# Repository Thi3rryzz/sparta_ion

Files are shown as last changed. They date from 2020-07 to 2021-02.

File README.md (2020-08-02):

Open Source Sparta ION
=============
There's a bunch of (Dutch) blog posts that go with this: (http://infant.tweakblogs.net/blog/cat/2875) (Awesome work InfantEudora)
Also check out the Discord: (https://discord.gg/anZees2)

This repository contains the following:

 folder       |  descr
--------------|-------------------------------------------------------------
 eagle        | All relevant eagle files, BOM lists.
 ion_firmware | AVR Studio projects for the different kinds of firmware.
 ion_software | Software for testing, or uploading hex files.
 lib          | Files used in either firmware or software.
 lib_ion      | Files used for Sparta ION specific code.

All files in this repository are released under GNU GPLv3 (https://www.gnu.org/copyleft/gpl.html)

Software used:
----------------
 - Atmel Studio 7.0.2397 (https://www.microchip.com/mplab/avr-support/atmel-studio-7)
 - GCC 9.3.0
 - Windows: Cygwin(https://cygwin.com/install.html)
 - Eagle 8.6.3 (http://www.cadsoftusa.com/)

Firmware:
----------------

The firmware running your bike's motor, consists of three parts:
 - A bootloader, started on powerup.
 - The actual firmware, called application executed by the bootloader.
 - Configuration memory, stored in ROM.

The bootloader uses two blocks to identify the harware it's running on, and what firmware should be loaded.
The firware uses one block to read/write settings, which are currently the strain gauge calibration.

If you wan't to build a control PCB, use the latest revision of 3phasecntrl.

New Hardare Revision Wishlist:
Motor Driver:
 - Modify 3phasecntrl for XHP motors.
BMS:
 - Modifiy BMS for Li-Ion/Li-Po support.

New Software Revision Wishlist:
 - Enhance CU3 Display support
 - Write BMS code
 - Modify Bootloader for BMS

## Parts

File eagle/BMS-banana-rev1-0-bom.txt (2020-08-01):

Part          Value                            Device                           Package              Description                             FARNELL LCSC    LSCS   MPN        OC_FARNELL OC_NEWARK PACKAGE               POPULARITY SPICEPREFIX SUPPLIER              
C1            4u7                              C-EUC0805                        C0805                CAPACITOR, European symbol                                                                                           88         C                                 
C2            100n                             C-EUC0805                        C0805                CAPACITOR, European symbol                                                                                           88         C                                 
C3            100n                             C-EUC0805                        C0805                CAPACITOR, European symbol                                                                                           88         C                                 
C4            22p                              C-EUC0805                        C0805                CAPACITOR, European symbol                                                                                           88         C                                 
C5            22p                              C-EUC0805                        C0805                CAPACITOR, European symbol                                                                                           88         C                                 
C6            10u/50V                          CPOL-EU153CLV-0605               153CLV-0605          POLARIZED CAPACITOR, European symbol                                                                                                                              
C7            33u/25V                          CPOL-EU153CLV-0605               153CLV-0605          POLARIZED CAPACITOR, European symbol                                                                                                                              
C8            10u/16V                          CPOL-EU153CLV-0405               153CLV-0405          POLARIZED CAPACITOR, European symbol                                                                                                                              
C9            1u                               C-EUC0805                        C0805                CAPACITOR, European symbol                                                                                           88         C                                 
C10           100n                             C-EUC0805                        C0805                CAPACITOR, European symbol                                                                                           88         C                                 
C11           10u/16V                          CPOL-EU153CLV-0405               153CLV-0405          POLARIZED CAPACITOR, European symbol                                                                                                                              
C12           100n                             C-EUC0805                        C0805                CAPACITOR, European symbol                                                                                           88         C                                 
C13           100n                             C-EUC0805                        C0805                CAPACITOR, European symbol                                                                                           88         C                                 
C14           100n                             C-EUC0805                        C0805                CAPACITOR, European symbol                                                                                           88         C                                 
C15           22u/16V                          C-EUC0805                        C0805                CAPACITOR, European symbol                                                                                           88         C                                 
C16           22u/16V                          C-EUC0805                        C0805                CAPACITOR, European symbol                                                                                           88         C                                 
C17           100n                             C-EUC0805                        C0805                CAPACITOR, European symbol                                                                                           88         C                                 
C18           22u/16V                          C-EUC0805                        C0805                CAPACITOR, European symbol                                                                                           88         C                                 
C19           100n                             C-EUC0805                        C0805                CAPACITOR, European symbol                                                                                           88         C                                 
C20           100n                             C-EUC0805                        C0805                CAPACITOR, European symbol                                                                                           88         C                                 
C21           100n                             C-EUC0805                        C0805                CAPACITOR, European symbol                                                                                           88         C                                 
C22           22p                              C-EUC0805                        C0805                CAPACITOR, European symbol                                                                                           88         C                                 
C23           DNP                              C-EUC0805                        C0805                CAPACITOR, European symbol                                                                                           88         C                                 
D1            BAT46WH                          DIODE-SMB                        SMB                  DIODE                                   2069340                                                                                                                   
D2            BAT46WH                          DIODE-SMB                        SMB                  DIODE                                   2069340                                                                                                                   
D3            BAT46WH                          DIODE-SMB                        SMB                  DIODE                                   2069340                                                                                                                   
D4            SM6T39A                          DIODE-SMB                        SMB                  DIODE                                   9802703                                                                                                                   
D5            BAT46WH                          DIODE-SOD323-W                   SOD323-W             DIODE                                                                                                                                                             
F1            1A                               PTCFUSE-1812                     1812                 PTC fuses, resettable thermistors                                                                                                                                 
F2            300mA                            PTCFUSE-1812                     1812                 PTC fuses, resettable thermistors                                                                                                                                 
F3            300mA                            PTCFUSE-1812                     1812                 PTC fuses, resettable thermistors                                                                                                                                 
IC4           LD1117S50                        LM340ST-ST                       SOT223               Positive VOLTAGE REGULATOR              1467780                                                                                                                   
IC6           LD1117S33                        LM340ST-ST                       SOT223               Positive VOLTAGE REGULATOR                                                                                                                                        
K1            SLA-12VDC-SL-A                   SLA-12VDC-SL-A                   SLA-12VDC-SL-A                                                               C55194                                                                                                    
K2            SLA-12VDC-SL-A                   SLA-12VDC-SL-A                   SLA-12VDC-SL-A                                                               C55194                                                                                                    
L1            150u/250mA                       L-USWE-TPC                       POWER-CHOKE_WE-TPC   INDUCTOR, American symbol                                                                                                                                         
L2            4.7uH/700mA                      L_0805                           L0805                                                                                                                                                                                  
LED1          Red                              LEDCHIPLED_0805                  CHIPLED_0805         LED                                                                                                                  52                                           
LED2          Green                            LEDCHIPLED_0805                  CHIPLED_0805         LED                                                                                                                  52                                           
Q1            2N7002                           2N7002                           SOT-23                                                                                                                                                                                 
Q2            2N7002                           2N7002                           SOT-23                                                                                                                                                                                 
Q3            Q13FC1350000400                  Q13FC1350000400                  CRYSTAL_3215                                                         C32346                                                                                                            
R1            1k                               R-EU_R0805                       R0805                RESISTOR, European symbol                                                                                            86         R                                 
R2            2R2                              R-EU_R0805                       R0805                RESISTOR, European symbol                                                                                            86         R                                 
R3            10r                              R-EU_R0805                       R0805                RESISTOR, European symbol                                                                                            86         R                                 
R4            390k                             R-EU_R0805                       R0805                RESISTOR, European symbol                                                                                            86         R                                 
R5            100k                             R-EU_R0805                       R0805                RESISTOR, European symbol                                                                                            86         R                                 
R6            1k                               R-EU_R0805                       R0805                RESISTOR, European symbol                                                                                            86         R                                 
R7            1k                               R-EU_R0805                       R0805                RESISTOR, European symbol                                                                                            86         R                                 
R8            4k7                              R-EU_R0805                       R0805                RESISTOR, European symbol                                                                                            86         R                                 
R9            100k                             R-EU_R0805                       R0805                RESISTOR, European symbol                                                                                            86         R                                 
R10           4k7                              R-EU_R0805                       R0805                RESISTOR, European symbol                                                                                            86         R                                 
R11           10k                              R-EU_R0805                       R0805                RESISTOR, European symbol                                                                                            86         R                                 
R12           10k                              R-EU_R0805                       R0805                RESISTOR, European symbol                                                                                            86         R                                 
R13           16k2                             R-EU_R0805                       R0805                RESISTOR, European symbol                                                                                            86         R                                 
R14           604k                             R-EU_R0805                       R0805                RESISTOR, European symbol                                                                                            86         R                                 
R15           5m 4W                            SHUNT_2728                       R2728                                                                                                                                                                                  
R16           10k                              R-EU_R0805                       R0805                RESISTOR, European symbol                                                                                            86         R                                 
R17           100r                             R-EU_R0805                       R0805                RESISTOR, European symbol                                                                                            86         R                                 
R18           100r                             R-EU_R0805                       R0805                RESISTOR, European symbol                                                                                            86         R                                 
R19           10k                              R-EU_R0805                       R0805                RESISTOR, European symbol                                                                                            86         R                                 
R20           1k                               R-EU_R0805                       R0805                RESISTOR, European symbol                                                                                            86         R                                 
R22           20k                              R-EU_R0805                       R0805                RESISTOR, European symbol                                                                                            86         R                                 
R23           130k                             R-EU_R0805                       R0805                RESISTOR, European symbol                                                                                            86         R                                 
R24           10k                              R-EU_R0805                       R0805                RESISTOR, European symbol                                                                                            86         R                                 
R25           10k                              R-EU_R0805                       R0805                RESISTOR, European symbol                                                                                            86         R                                 
R26           390k                             R-EU_R0805                       R0805                RESISTOR, European symbol                                                                                            86         R                                 
R27           100k                             R-EU_R0805                       R0805                RESISTOR, European symbol                                                                                            86         R                                 
R28           390k                             R-EU_R0805                       R0805                RESISTOR, European symbol                                                                                            86         R                                 
R29           220k                             R-EU_R0805                       R0805                RESISTOR, European symbol                                                                                            86         R                                 
R30           100r                             R-EU_R0805                       R0805                RESISTOR, European symbol                                                                                            86         R                                 
R31           100r                             R-EU_R0805                       R0805                RESISTOR, European symbol                                                                                            86         R                                 
R32           100k                             R-EU_R0805                       R0805                RESISTOR, European symbol                                                                                            86         R                                 
R33           100k                             R-EU_R0805                       R0805                RESISTOR, European symbol                                                                                            86         R                                 
R34           1k                               R-EU_R0805                       R0805                RESISTOR, European symbol                                                                                            86         R                                 
R35           1k                               R-EU_R0805                       R0805                RESISTOR, European symbol                                                                                            86         R                                 
R36           10k                              R-EU_R0805                       R0805                RESISTOR, European symbol                                                                                            86         R                                 
R37           10k                              R-EU_R0805                       R0805                RESISTOR, European symbol                                                                                            86         R                                 
R38           10k                              R-EU_R0805                       R0805                RESISTOR, European symbol                                                                                            86         R                                 
R40           3k9                              R-EU_R0805                       R0805                RESISTOR, European symbol                                                                                            86         R                                 
R41           10k                              R-EU_R0805                       R0805                RESISTOR, European symbol                                                                                            86         R                                 
R43           1k                               R-EU_R0805                       R0805                RESISTOR, European symbol                                                                                            86         R                                 
RT1           NTC_0805                         NTC_0805                         R0805                                                                                                                                                                                  
T1            BC847                            BC847                            SOT23                NPN TRANSISTOR                                                                                                                                                    
T2            BC847                            BC847                            SOT23                NPN TRANSISTOR                                                                                                                                                    
U$1           AVR-PDIVERT                      AVR-PDIVERT                      AVR-ISP-6            AVR PDI programming interface connector                                                                                                                           
U$2           TSX-3225                         TSX-3225                         TSX-3225                                                                                                                                                                               
U1            ATXMEGA32A4U-AU                  ATXMEGA32A4U-AU                  TQFP-44A-44          8/16-bit XMEGA A4U Microcontroller                                                                                                                                
U2            LM5008MM                         LM5008MM                         SOP65P490X109-8N     Step-Down Switching Regulator                                  LM5008MM   8181721    38K3760   SOP-8                                        National Semiconductor
U3            BQ34Z100                         BQ34Z100                         PW_R-PDSO-G14                                                                                                                                                                          
U4            JW5033S                          JW5033S                          SOT23-6                                                              C324577                                                                                                           
U5            PCF8563                          PCF8563                          SO08                                                                 C7440                                                                                                             
U6            90325-0008                       90325-0008                       MOLEX_90325-0008     HEADER                                                         90325-0008 673237     46WX960   HEADER, 1.27MM, 8 WAY                        Molex

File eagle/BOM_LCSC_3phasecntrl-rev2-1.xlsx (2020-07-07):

LCSC Part Number | Manufacture Part Number | Manufacturer | Customer NO. | Package | Description | RoHS | Order Qty. | Min\Mult Order Qty. | Unit Price | Order Price
C1779 | CL21A475KAQNNNE | Samsung Electro-Mechanics |  | 0805 | Multilayer Ceramic Capacitors MLCC - SMD/SMT 4.7uF 25V 0805 RoHS | Yes | 20 | 20\20 | $0.016685 | $0.33
C2316 | XH-3A | BOOMELE(Boom Precision Elec) |  | Through Hole | Wire To Board / Wire To Wire Connector Through Hole RoHS | Yes | 50 | 50\50 | $0.00584 | $0.29
C2318 | XH-5A | BOOMELE(Boom Precision Elec) |  | Through Hole | Wire To Board / Wire To Wire Connector Through Hole RoHS | Yes | 50 | 50\50 | $0.009577 | $0.48
C5670 | XH-T | BOOMELE(Boom Precision Elec) |  | - | Terminals RoHS | Yes | 200 | 100\100 | $0.003339 | $0.67
C10384 | XH-7A | BOOMELE(Boom Precision Elec) |  | Through Hole | Wire To Board / Wire To Wire Connector Through Hole RoHS | Yes | 50 | 50\50 | $0.01369 | $0.68
C10387 | XH-3Y | BOOMELE(Boom Precision Elec) |  | Housing | Rectangular Connectors Housings Housing RoHS | Yes | 100 | 100\100 | $0.002335 | $0.23
C10388 | XH-5Y | BOOMELE(Boom Precision Elec) |  | Housing | Rectangular Connectors Housings Housing RoHS | Yes | 50 | 50\50 | $0.004063 | $0.2
C16906 | XH-7Y | BOOMELE(Boom Precision Elec) |  | Housing | Rectangular Connectors Housings Housing RoHS | Yes | 50 | 50\50 | $0.005804 | $0.29
C17656 | 0805W8F3903T5E | UNI-ROYAL(Uniroyal Elec) |  | 0805 | Chip Resistor - Surface Mount 390KOhms ±1% 1/8W 0805 RoHS | Yes | 100 | 100\100 | $0.002323 | $0.23
C24658 | 0805CG220J500NT | FH(Guangdong Fenghua Advanced Tech) |  | 0805 | Multilayer Ceramic Capacitors MLCC - SMD/SMT 22pF 50V 0805 RoHS | Yes | 50 | 50\50 | $0.007677 | $0.38
C25278 | 0805W8J0100T5E | UNI-ROYAL(Uniroyal Elec) |  | 0805 | Chip Resistor - Surface Mount 10Ohms ±5% 1/8W 0805 RoHS | Yes | 100 | 100\100 | $0.001585 | $0.16
C25301 | 0805W8J022JT5E | UNI-ROYAL(Uniroyal Elec) |  | 0805 | Chip Resistor - Surface Mount 2.2Ohms ±5% 1/8W 0805 RoHS | Yes | 100 | 100\100 | $0.001626 | $0.16
C25611 | 0805W8J0104T5E | UNI-ROYAL(Uniroyal Elec) |  | 0805 | Chip Resistor - Surface Mount 100KOhms ±5% 1/8W 0805 RoHS | Yes | 100 | 100\100 | $0.00174 | $0.17
C25612 | 0805W8J0103T5E | UNI-ROYAL(Uniroyal Elec) |  | 0805 | Chip Resistor - Surface Mount 10KOhms ±5% 1/8W 0805 RoHS | Yes | 100 | 100\100 | $0.001708 | $0.17
C35879 | LD1117S33CTR | STMicroelectronics |  | SOT-223 | Low Dropout Regulators(LDO) positive Fixed 1.3V @ 800mA 15V 3.3V 800mA SOT-223 RoHS | Yes | 3 | 1\1 | $0.17298 | $0.52
C72037 | 17-21SURC/S530-A3/TR8 | Everlight Elec |  | 0805 | Light Emitting Diodes (LED) Red 624~632nm 60mcd Surface Mount 0805 RoHS | Yes | 20 | 20\20 | $0.014482 | $0.29
C72508 | RVT1V330M0605 | ROQANG |  | SMD,6.3x5.4mm | Aluminum Electrolytic Capacitors - SMD 33uF ±20% 35V SMD,6.3x5.4mm RoHS | Yes | 20 | 20\20 | $0.030069 | $0.6
C81157 | LD1117S50CTR | STMicroelectronics |  | SOT-223 | Low Dropout Regulators(LDO) positive Fixed 1.3V @ 800mA 15V 5V 800mA SOT-223 RoHS | Yes | 3 | 1\1 | $0.182207 | $0.55
C115302 | RS-05K102JT | FH(Guangdong Fenghua Advanced Tech) |  | 0805 | Chip Resistor - Surface Mount 1KOhms ±5% 1/8W 0805 RoHS | Yes | 100 | 100\100 | $0.001646 | $0.16
C115310 | RS-05K472JT | FH(Guangdong Fenghua Advanced Tech) |  | 0805 | Chip Resistor - Surface Mount 4.7KOhms ±5% 1/8W 0805 RoHS | Yes | 100 | 100\100 | $0.001628 | $0.16
C119076 | RS-05K471JT | FH(Guangdong Fenghua Advanced Tech) |  | 0805 | Chip Resistor - Surface Mount 470Ohms ±5% 1/8W 0805 RoHS | Yes | 100 | 100\100 | $0.001726 | $0.17
C123821 | SMBJ43A | MDD（Microdiode Electronics） |  | SMB(DO-214AA) | TVS SMB(DO-214AA) RoHS | Yes | 10 | 10\10 | $0.050743 | $0.51
C181140 | BC847B | Guangdong Hottech |  | SOT-23(SOT-23-3) | Transistors (NPN/PNP) NPN 100mA 45V SOT-23(SOT-23-3) RoHS | Yes | 50 | 50\50 | $0.007022 | $0.35
C205442 | ORH-G35A | Orient |  | 0805 | Light Emitting Diodes (LED) Green 515~535nm 80mcd@5mA Surface Mount 0805 RoHS | Yes | 50 | 50\50 | $0.013399 | $0.67
C191876 | LM5008MM/NOPB | Texas Instruments |  | VSSOP-8 | DC-DC Converters Step-Down Adjustable 1 9.5V 95V 2.5V 75V 350mA VSSOP-8 RoHS | Yes | 3 | 1\1 | $1.064318 | $3.19
C220600 | ATXMEGA32A4U-ANR | Microchip Tech |  | TQFP-44_10x10x08P | ATMEL & AVR TQFP-44_10x10x08P RoHS | Yes | 2 | 1\1 | $4.325682 | $8.65
C249566 | VEJ100M1ETR-0405 | Lelon |  | SMD,4x5.3mm | Aluminum Electrolytic Capacitors - SMD 10uF ±20% 25V SMD,4x5.3mm RoHS | Yes | 10 | 10\10 | $0.050009 | $0.5
C262019 | TLC-MSMD014 | TLC Electronic |  | 1812 | PTC Resettable Fuses 1812 RoHS | Yes | 10 | 10\10 | $0.039863 | $0.4
C271394 | VH1H100ME054000CE0 | Changzhou Huawei Elec |  | SMD,6.3x5.4mm | Aluminum Electrolytic Capacitors - SMD 10uF ±20% 50V SMD,6.3x5.4mm RoHS | Yes | 10 | 10\10 | $0.042309 | $0.42
C283866 | SMF3.3A | DOWO |  | SOD-123 | TVS SOD-123 RoHS | Yes | 10 | 10\10 | $0.06265 | $0.63
C294696 | RS-05K224JT | FH(Guangdong Fenghua Advanced Tech) |  | 0805 | Chip Resistor - Surface Mount 220KOhms ±5% 1/8W 0805 RoHS | Yes | 100 | 100\100 | $0.001619 | $0.16
C326345 | SNR6045K-151M | 3L COILS |  | SMD,6.0x6.0mm | Inductors (SMD) SMD,6.0x6.0mm RoHS | Yes | 2 | 1\1 | $0.132586 | $0.27
C387369 | S3D16.000000B20F30T | Shenzhen SCTF Elec |  | SMD-3225-4P | SMD Oscillators(XO) 16MHz ±20ppm SMD-3225-4P RoHS | Yes | 2 | 1\1 | $0.485227 | $0.97
C426768 | BAT46WH,115 | Nexperia |  | SOD-123F | Schottky Barrier Diodes (SBD) SOD-123F RoHS | Yes | 10 | 5\5 | $0.07098 | $0.71
C495959 | C0805X104K101TB | IHHEC(HOLY STONE ENTERPRISE CO., LTD) |  | 0805 | Multilayer Ceramic Capacitors MLCC - SMD/SMT 100nF 100V 0805 RoHS | Yes | 200 | 20\20 | $0.015113 | $3.02

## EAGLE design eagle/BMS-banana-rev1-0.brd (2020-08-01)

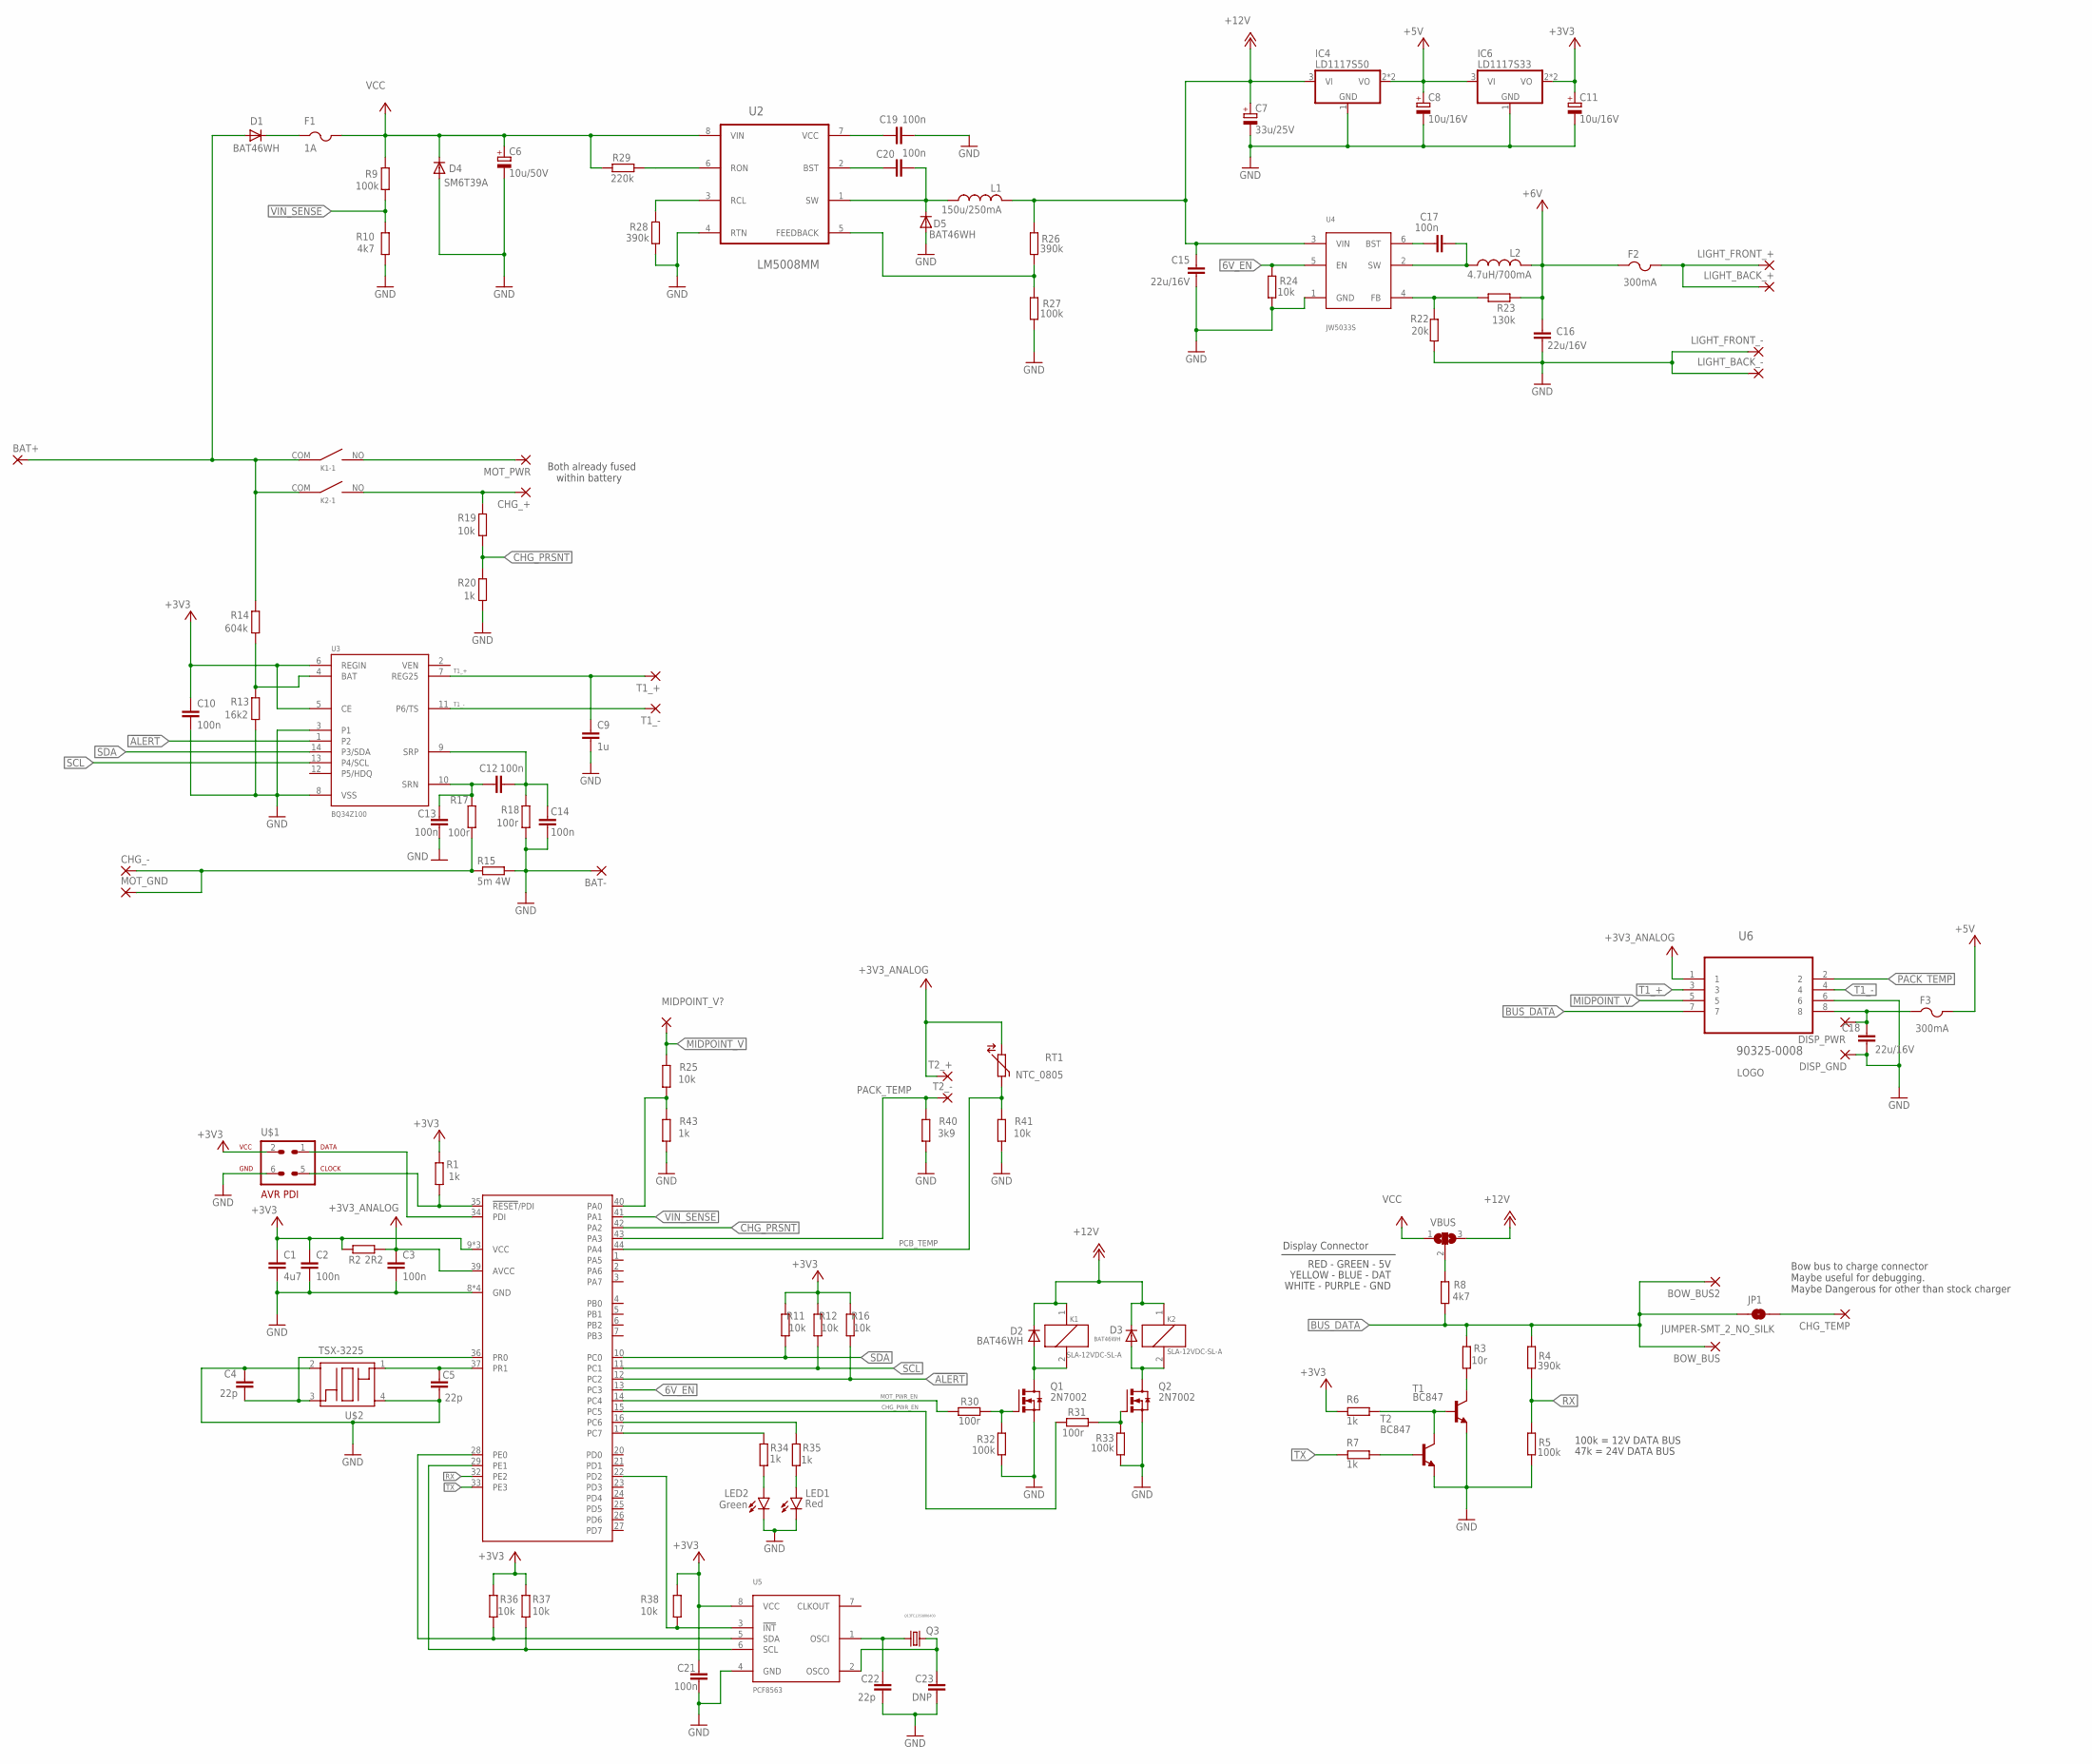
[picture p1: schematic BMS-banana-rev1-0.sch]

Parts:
BAT+: 3,81/2,1
BAT-: 3,81/2,1
BOW_BUS: 3,81/2,1
BOW_BUS2: 2,54/0,8
C1: 4u7; C0805
C2, C3, C10, C12, C13, C14, C17, C19, C20, C21: 100n; C0805
C4, C5, C22: 22p; C0805
C6: 10u/50V; 153CLV-0605
C7: 33u/25V; 153CLV-0605
C8, C11: 10u/16V; 153CLV-0405
C9: 1u; C0805
C15, C16, C18: 22u/16V; C0805
C23: DNP; C0805
CHG_+: 3,81/2,1
CHG_-: 3,81/2,1
CHG_TEMP: 3,81/2,1
D1, D2, D3: BAT46WH; SMB; FARNELL 2069340
D4: SM6T39A; SMB; FARNELL 9802703
D5: BAT46WH; SOD323-W
DISP_GND: 2,54/0,8
DISP_PWR: 2,54/0,8
F1: 1A; 1812
F2, F3: 300mA; 1812
IC4: LD1117S50; SOT223; FARNELL 1467780
IC6: LD1117S33; SOT223
JP1: JUMPER-SMT_2_NO_SILK; SMT-JUMPER_2_NO_SILK
K1, K2: SLA-12VDC-SL-A
L1: 150u/250mA; POWER-CHOKE_WE-TPC
L2: 4.7uH/700mA; L0805
LED1: Red; CHIPLED_0805
LED2: Green; CHIPLED_0805
LIGHT_BACK_+: 2,54/0,8
LIGHT_BACK_-: 2,54/0,8
LIGHT_FRONT_+: 2,54/0,8
LIGHT_FRONT_-: 2,54/0,8
MIDPOINT_V?: 2,54/0,8
MOT_GND: 3,81/2,1
MOT_PWR: 3,81/2,1
Q1, Q2: 2N7002; SOT-23
Q3: Q13FC1350000400; CRYSTAL_3215
R1, R6, R7, R20, R34, R35, R43: 1k; R0805
R2: 2R2; R0805
R3: 10r; R0805
R4, R26, R28: 390k; R0805
R5, R9, R27, R32, R33: 100k; R0805
R8, R10: 4k7; R0805
R11, R12, R16, R19, R24, R25, R36, R37, R38, R41: 10k; R0805
R13: 16k2; R0805
R14: 604k; R0805
R15: 5m 4W; R2728
R17, R18, R30, R31: 100r; R0805
R22: 20k; R0805
R23: 130k; R0805
R29: 220k; R0805
R40: 3k9; R0805
RT1: NTC_0805; R0805
T1, T2: BC847; SOT23
T1_+, T1_-, T2_+, T2_-: 2,54/0,8
U1: ATXMEGA32A4U-AU; TQFP-44A-44
U2: LM5008MM; SOP65P490X109-8N
U3: BQ34Z100; PW_R-PDSO-G14
U4: JW5033S; SOT23-6
U5: PCF8563; SO08
U6: 90325-0008; MOLEX_90325-0008
U$1: AVR-PDIVERT; AVR-ISP-6
U$2: TSX-3225
U$4: AFROBOTICLOGOAFROBOTICLOGO_SMALL; AFROBOTICLOGOSMALL
VBUS: SJ2W; SJ_2

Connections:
6V_EN: R24.2, U1.13 (PC3), U4.5 (EN)
!ALERT: R16.1, U1.12 (PC2), U3.1 (P2)
+3V3: C1.1, C2.1, C10.1, C11.+, C21.2, IC6.2 (VO), IC6.4 (VO), R1.2, R2.2, R6.2, R11.2, R12.2, R16.2, R36.2, R37.2, R38.2, U1.9 (VCC), U1.19 (VCC), U1.31 (VCC), U3.5 (CE), U3.6 (REGIN), U5.8 (VCC), U$1.2
+3V3_ANALOG: C3.1, R2.1, RT1.2, T2_+.1, U1.39 (AVCC), U6.1
+5V: C8.+, F3.2, IC4.2 (VO), IC4.4 (VO), IC6.3 (VI)
+6V: C16.2, F2.1, L2.2, R23.1
+12V: C7.+, C15.2, D2.C, D3.C, IC4.3 (VI), K1.1, K2.1, L1.2, R26.2, U4.3 (VIN), VBUS.3
BUS_DATA: BOW_BUS.1, BOW_BUS2.1, JP1.1, R3.2, R4.2, R8.1, U6.7
CHG_PRSNT: R19.1, R20.2, U1.42 (PA2)
CHG_PWR_EN: R31.1, U1.15 (PC5)
GND: BAT-.1, C1.2, C2.2, C3.2, C4.1, C5.2, C6.-, C7.-, C8.-, C9.2, C10.2, C11.-, C13.1, C14.1, C15.1, C16.1, C18.1, C19.2, C21.1, C22.1, C23.1, D4.A, D5.A, DISP_GND.1, IC4.1 (GND), IC6.1 (GND), LED1.C, LED2.C, LIGHT_BACK_-.1, LIGHT_FRONT_-.1, Q1.2 (S), Q2.2 (S), R5.1, R10.1, R13.1, R15.P$2 (2), R18.1, R20.1, R22.1, R24.1, R27.1, R28.1, R32.2, R33.2, R40.1, R41.1, R43.1, T1.2 (E), T2.2 (E), U1.8 (GND), U1.18 (GND), U1.30 (GND), U1.38 (GND), U2.4 (RTN), U3.3 (P1), U3.8 (VSS), U4.1 (GND), U5.4 (GND), U6.6, U$1.6, U$2.2 (GND_2), U$2.4 (GND_4)
MIDPOINT_V: MIDPOINT_V?.1, R25.2, U6.5
MOT_PWR_EN: R30.2, U1.14 (PC4)
unnamed: R1.1, U1.35 (!RESET!/PDI), U$1.5
unnamed: U1.34 (PDI), U$1.1
unnamed: D1.C, F1.1
unnamed: C5.1, U1.37 (PR1), U$2.1 (XTALIN)
unnamed: C4.2, U1.36 (PR0), U$2.3 (XTALOUT)
unnamed: R8.2, VBUS.2
unnamed: C19.1, U2.7 (VCC)
unnamed: R13.2, R14.1, U3.4 (BAT)
unnamed: R22.2, R23.2, U4.4 (FB)
unnamed: CHG_-.1, MOT_GND.1, R15.P$1 (1), R17.1
unnamed: R3.1, T1.3 (C)
unnamed: C12.1, C13.2, R17.2, U3.10 (SRN)
unnamed: CHG_+.1, K2.NO, R19.2
unnamed: C12.2, C14.2, R18.2, U3.9 (SRP)
unnamed: C20.1, U2.2 (BST)
unnamed: K1.NO, MOT_PWR.1
unnamed: CHG_TEMP.1, JP1.2
unnamed: F2.2, LIGHT_BACK_+.1, LIGHT_FRONT_+.1
unnamed: C18.2, DISP_PWR.1, F3.1, U6.8
unnamed: C20.2, D5.C, L1.1, U2.1 (SW)
unnamed: R7.1, T2.1 (B)
unnamed: R26.1, R27.2, U2.5 (FEEDBACK)
unnamed: R6.1, T1.1 (B), T2.3 (C)
unnamed: C17.1, U4.6 (BST)
unnamed: R28.2, U2.3 (RCL)
unnamed: C17.2, L2.1, U4.2 (SW)
unnamed: R25.1, R43.2, U1.40 (PA0)
unnamed: R29.1, U2.6 (RON)
unnamed: Q1.1 (G), R30.1, R32.1
unnamed: D2.A, K1.2, Q1.3 (D)
unnamed: R38.1, U1.22 (PD2), U5.3 (!INT)
unnamed: D3.A, K2.2, Q2.3 (D)
unnamed: Q2.1 (G), R31.2, R33.1
unnamed: LED2.A, R34.1
unnamed: R37.1, U1.29 (PE1), U5.6 (SCL)
unnamed: LED1.A, R35.1
unnamed: R35.2, U1.16 (PC6)
unnamed: R34.2, U1.17 (PC7)
unnamed: R36.1, U1.28 (PE0), U5.5 (SDA)
unnamed: C22.2, Q3.P$1 (1), U5.1 (OSCI)
unnamed: C23.2, Q3.P$2 (2), U5.2 (OSCO)
PACK_TEMP: R40.2, T2_-.1, U1.43 (PA3), U6.2
PCB_TEMP: R41.2, RT1.1, U1.44 (PA4)
RX: R4.1, R5.2, U1.32 (PE2)
SCL: R12.1, U1.11 (PC1), U3.13 (P4/SCL)
SDA: R11.1, U1.10 (PC0), U3.14 (P3/SDA)
T1_+: C9.1, T1_+.1, U3.7 (REG25), U6.3
T1_-: T1_-.1, U3.11 (P6/TS), U6.4
TX: R7.2, U1.33 (PE3)
VBAT: BAT+.1, D1.A, K1.COM, K2.COM, R14.2
VCC: C6.+, D4.C, F1.2, R9.2, R29.2, U2.8 (VIN), VBUS.1
VIN_SENSE: R9.1, R10.2, U1.41 (PA1)

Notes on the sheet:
RED - GREEN - 5V
WHITE - PURPLE - GND
YELLOW - BLUE - DAT
Display Connector
100k = 12V DATA BUS
47k = 24V DATA BUS
Both already fused within battery
Bow bus to charge connector Maybe useful for debugging. Maybe Dangerous for other than stock charger

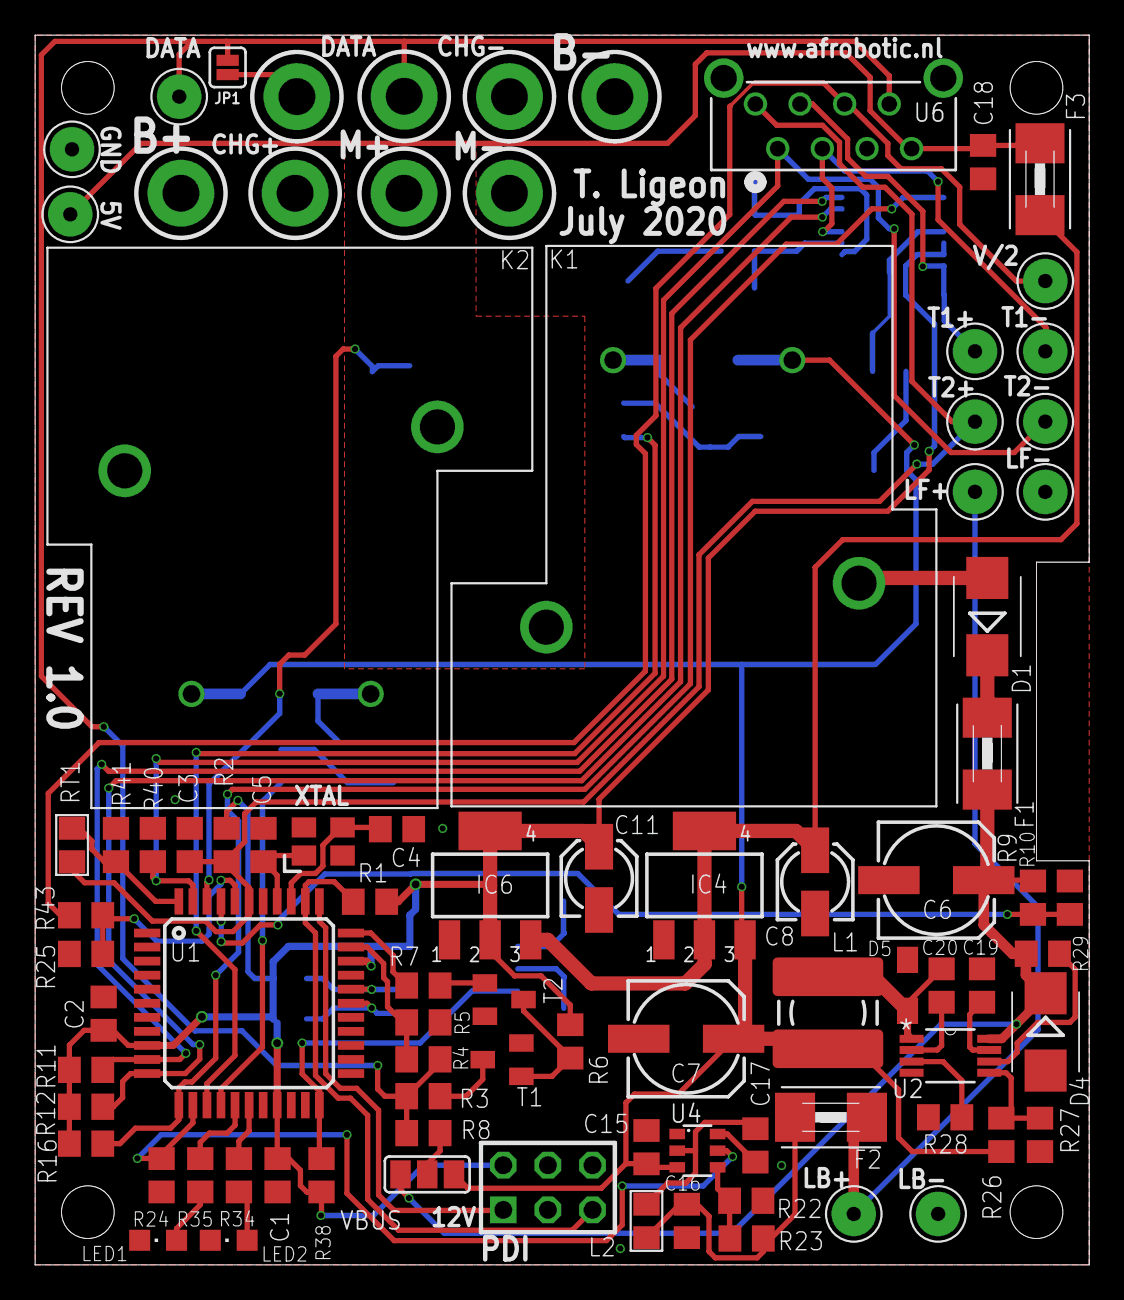
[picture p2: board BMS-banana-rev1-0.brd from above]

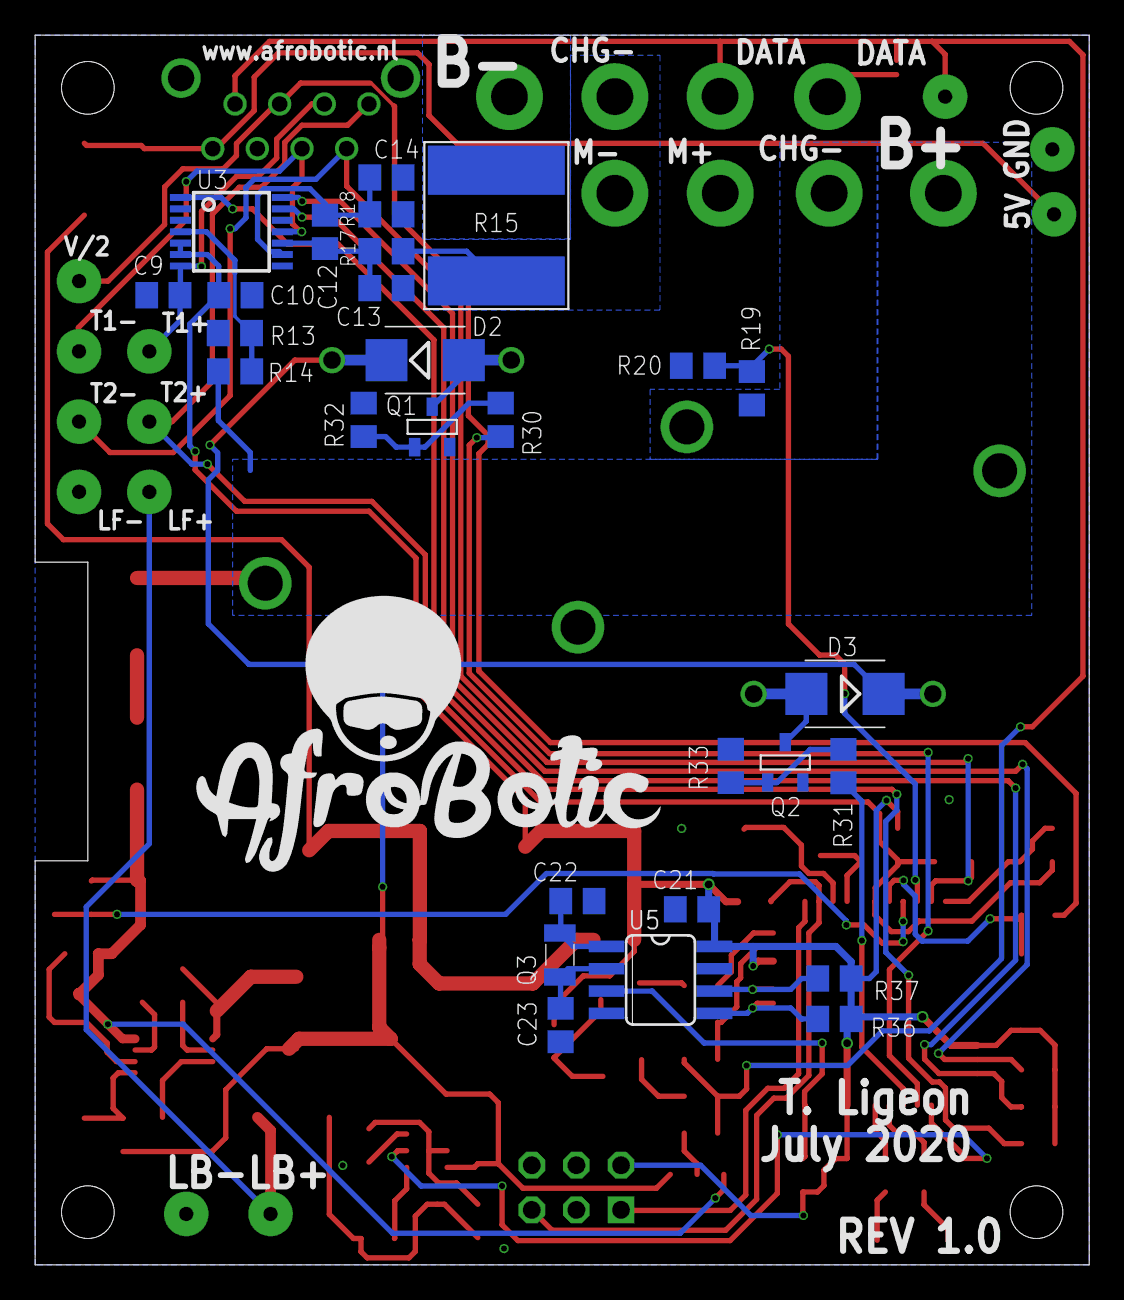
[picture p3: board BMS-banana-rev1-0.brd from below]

Board: 2 copper layers, 60.0 x 70.0 mm, 116 parts (29 on the bottom side), 65 nets.

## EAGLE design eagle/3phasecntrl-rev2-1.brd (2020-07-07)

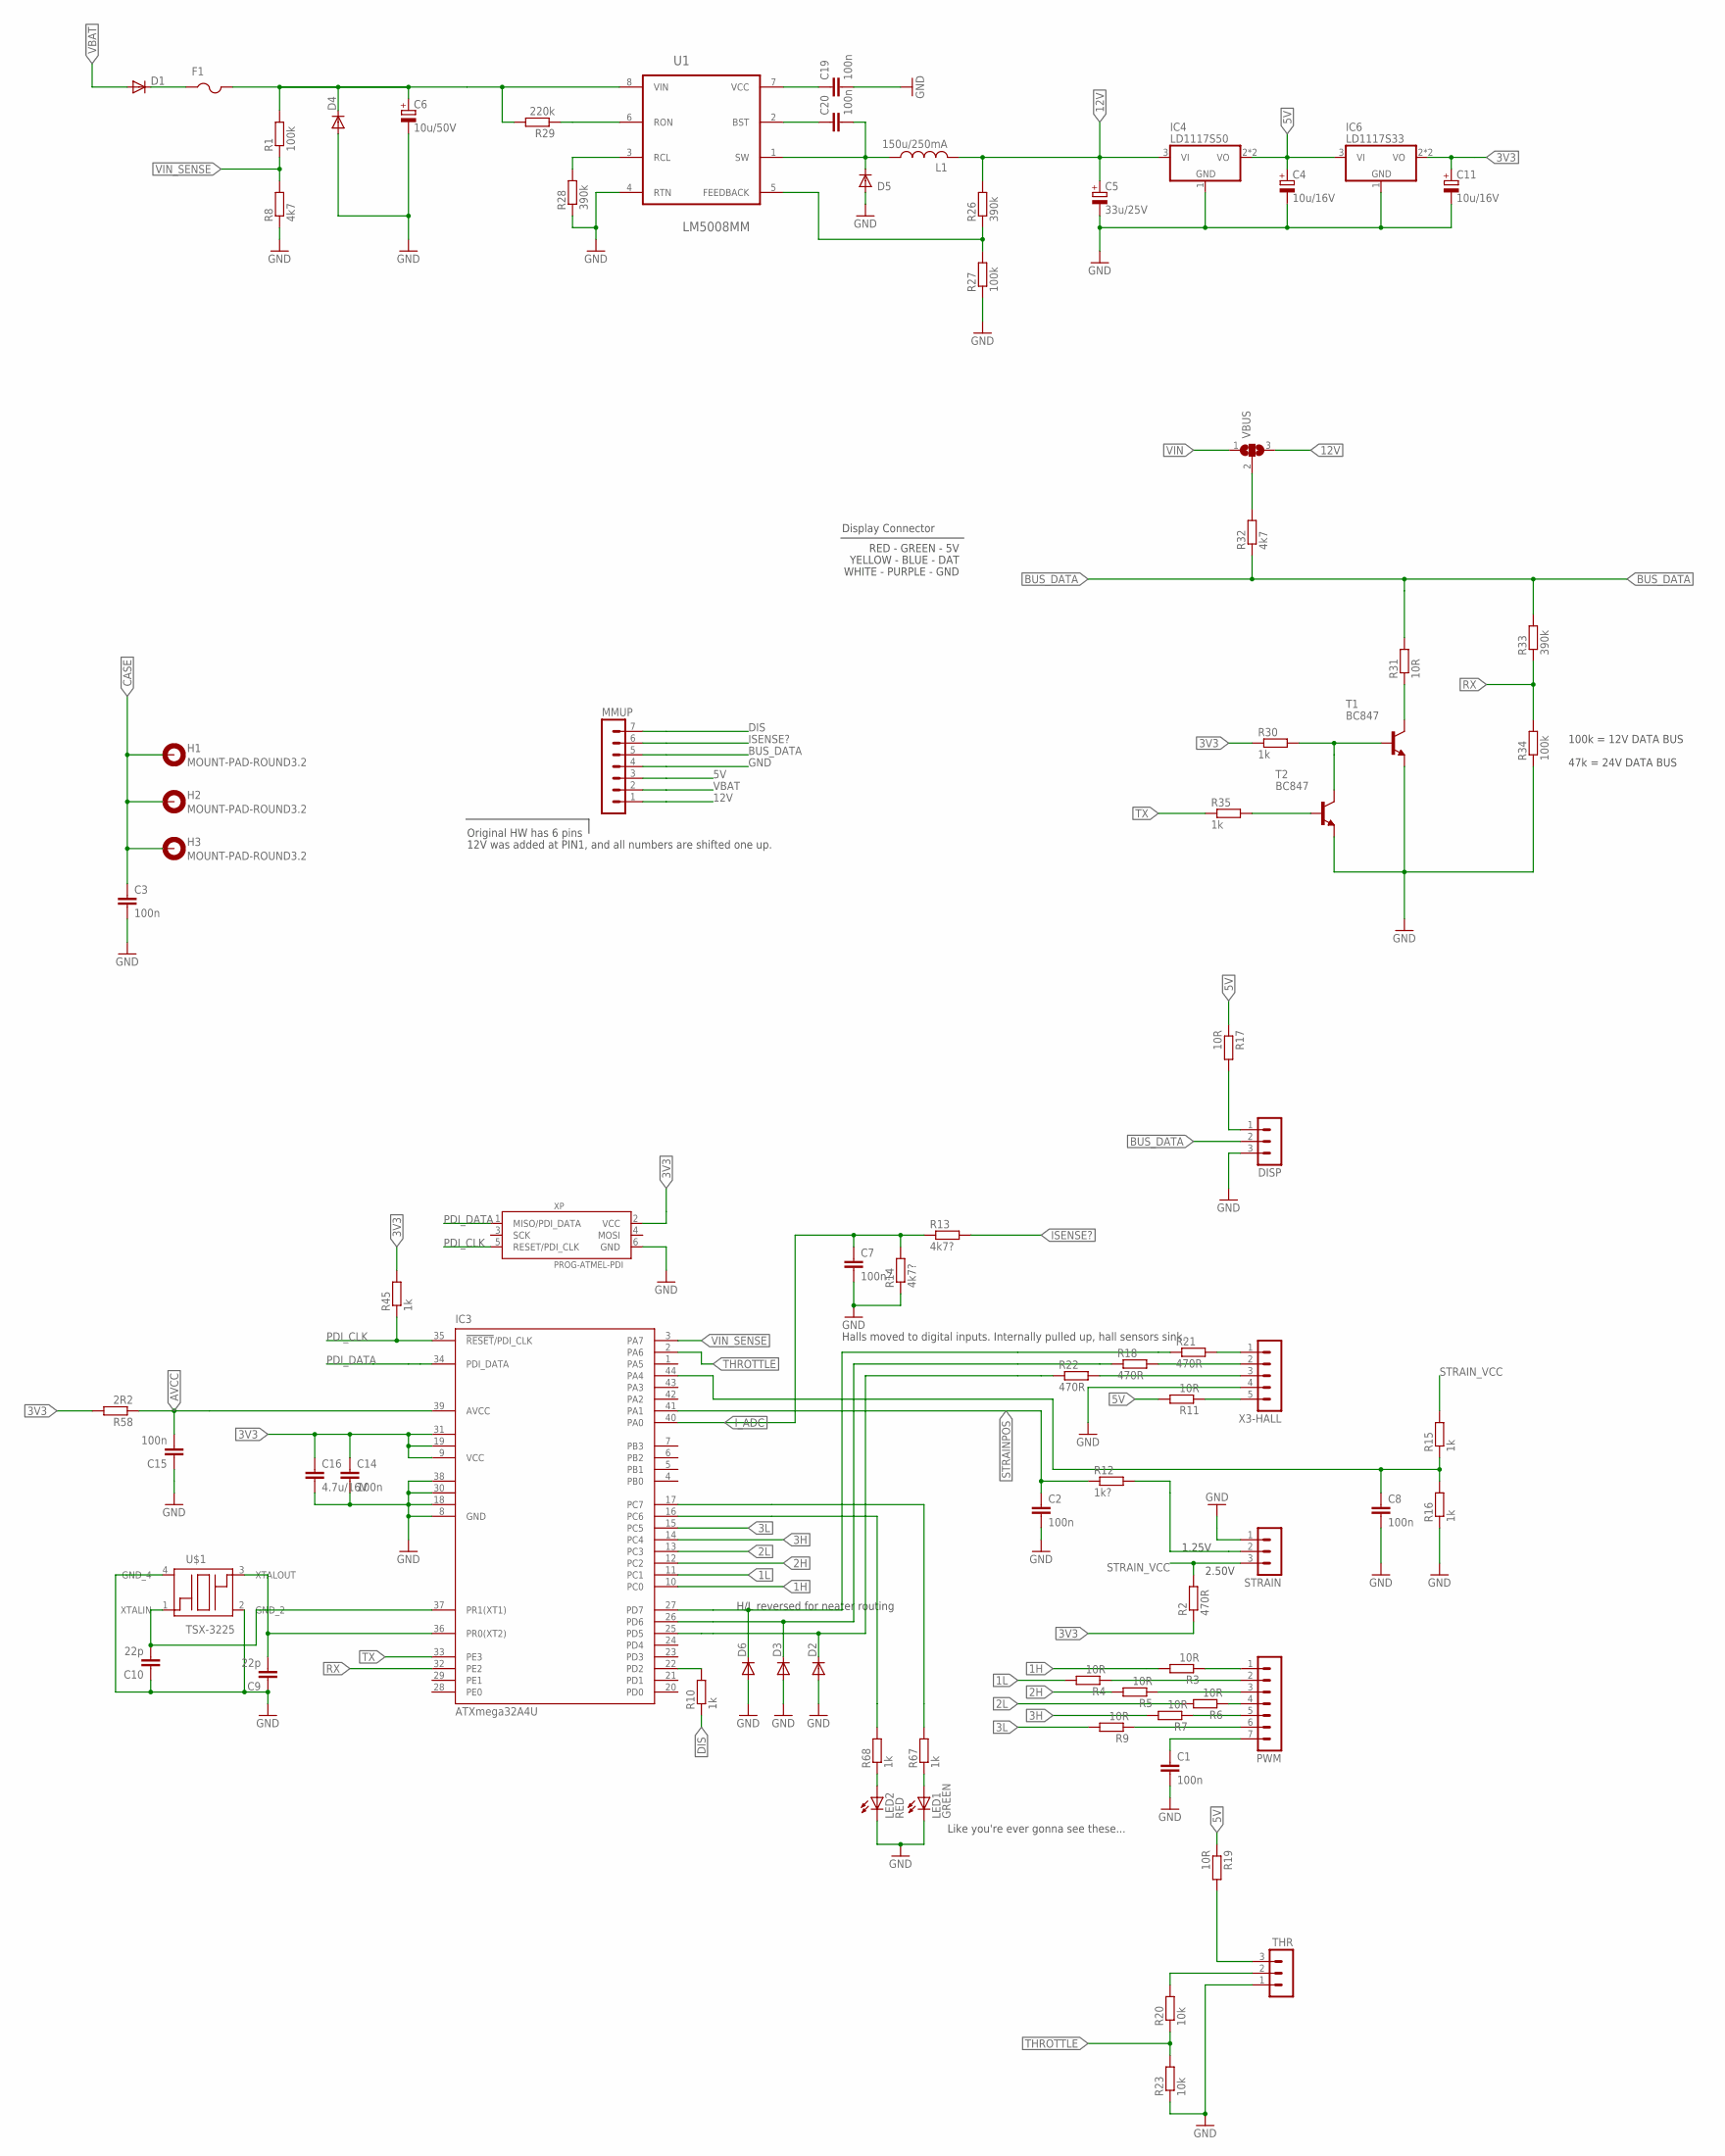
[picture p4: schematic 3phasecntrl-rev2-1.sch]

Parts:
C1, C2, C3, C8, C14, C15, C19, C20: 100n; C0805K
C4, C11: 10u/16V; 153CLV-0405
C5: 33u/25V; 153CLV-0605
C6: 10u/50V; 153CLV-0605
C7: 100n?; C0805K
C9, C10: 22p; C0805K
C16: 4.7u/16V; C0805K
D1: BAT46WH; SMB; FARNELL 2069340
D2, D3, D6: PTVS3V3S1UTR; SOD123; FARNELL 2575110
D4: SM6T39A; SMB; FARNELL 9802703
D5: BAT46WH; SOD323-W
DISP: MA03-1
F1: PTCFUSE-1812; 1812
H1, H2, H3: MOUNT-PAD-ROUND3.2; 3,2-PAD
IC3: ATXmega32A4U; TQFP44
IC4: LD1117S50; SOT223; FARNELL 1467780
IC6: LD1117S33; SOT223
L1: 150u/250mA; POWER-CHOKE_WE-TPC
LED1: GREEN; CHIPLED_0805
LED2: RED; CHIPLED_0805
MMUP: MA07-1
PWM: MA07-1
R1, R27, R34: 100k; M0805
R2, R18, R21, R22: 470R; M0805
R3, R4, R5, R6, R7, R9, R11, R17, R19, R31: 10R; M0805
R8, R32: 4k7; M0805
R10, R15, R16, R30, R35, R67, R68: 1k; M0805
R12: 1k?; M0805
R13, R14: 4k7?; M0805
R20, R23: 10k; M0805
R26, R28, R33: 390k; M0805
R29: 220k; M0805
R45: 1k; R0805
R58: 2R2; R0805
STRAIN: MA03-1
T1, T2: BC847; SOT23
THR: MA03-1
U1: LM5008MM; SOP65P490X109-8N
U$1: TSX-3225
VBUS: SJ2W; SJ_2
X3-HALL: MA05-1
XP: PROG-ATMEL-PDI; 6-LSTB2

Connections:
1H: IC3.10 (PC0), R3.2
1L: IC3.11 (PC1), R4.2
2H: IC3.12 (PC2), R5.2
2L: IC3.13 (PC3), R6.2
3H: IC3.14 (PC4), R7.2
3L: IC3.15 (PC5), R9.2
3V3: C11.+, C14.1, C16.1, IC3.9 (VCC), IC3.19 (VCC1), IC3.31 (VCC2), IC6.2 (VO), IC6.4 (VO), R2.1, R30.1, R45.2, R58.2, XP.2 (VCC)
5V: C4.+, IC4.2 (VO), IC4.4 (VO), IC6.3 (VI), MMUP.3, R11.2, R17.1, R19.1
12V: C5.+, IC4.3 (VI), L1.2, MMUP.1, R26.2, VBUS.3
AVCC: C15.2, IC3.39 (AVCC), R58.1
BUS_DATA: DISP.2, MMUP.5, R31.2, R32.1, R33.2
CASE: C3.1, H1.B3,2, H2.B3,2, H3.B3,2
DIS: MMUP.7, R10.1
GND: C1.2, C2.2, C3.2, C4.-, C5.-, C6.-, C7.2, C8.2, C9.1, C10.1, C11.-, C14.2, C15.1, C16.2, C19.2, D2.A, D3.A, D4.A, D5.A, D6.A, DISP.3, IC3.8 (GND), IC3.18 (GND1), IC3.30 (GND2), IC3.38 (GND3), IC4.1 (GND), IC6.1 (GND), LED1.C, LED2.C, MMUP.4, R8.1, R14.1, R16.1, R23.1, R27.1, R28.1, R34.1, STRAIN.1, T1.2 (E), T2.2 (E), THR.1, U1.4 (RTN), U$1.2 (GND_2), U$1.4 (GND_4), X3-HALL.4, XP.6 (GND)
ISENSE?: MMUP.6, R13.2
I_ADC: C7.1, IC3.40 (PA0), R13.1, R14.2
unnamed: C1.1, PWM.7
unnamed: D1.C, F1.1
unnamed: C19.1, U1.7 (VCC)
unnamed: PWM.1, R3.1
unnamed: R12.2, STRAIN.2
unnamed: R32.2, VBUS.2
unnamed: IC3.22 (PD2), R10.2
unnamed: R11.1, X3-HALL.5
unnamed: R21.2, X3-HALL.1
unnamed: PWM.2, R4.1
unnamed: R18.2, X3-HALL.2
unnamed: R31.1, T1.3 (C)
unnamed: R22.2, X3-HALL.3
unnamed: C10.2, IC3.37 (PR1(XT1)), U$1.1 (XTALIN)
unnamed: LED1.A, R67.1
unnamed: LED2.A, R68.1
unnamed: C20.1, U1.2 (BST)
unnamed: R19.2, THR.3
unnamed: D6.C, IC3.27 (PD7), R21.1
unnamed: IC3.16 (PC6), R68.2
unnamed: IC3.17 (PC7), R67.2
unnamed: C20.2, D5.C, L1.1, U1.1 (SW)
unnamed: R35.2, T2.1 (B)
unnamed: R26.1, R27.2, U1.5 (FEEDBACK)
unnamed: R30.2, T1.1 (B), T2.3 (C)
unnamed: D3.C, IC3.26 (PD6), R18.1
unnamed: R28.2, U1.3 (RCL)
unnamed: PWM.3, R5.1
unnamed: PWM.4, R6.1
unnamed: R29.1, U1.6 (RON)
unnamed: D2.C, IC3.25 (PD5), R22.1
unnamed: PWM.5, R7.1
unnamed: PWM.6, R9.1
unnamed: DISP.1, R17.2
unnamed: C9.2, IC3.36 (PR0(XT2)), U$1.3 (XTALOUT)
PDI_CLK: IC3.35 (!RESET!/PDI_CLK), R45.1, XP.5 (RESET/PDI_CLK)
PDI_DATA: IC3.34 (PDI_DATA), XP.1 (MISO/PDI_DATA)
RX: IC3.32 (PE2), R33.1, R34.2
STRAINPOS: C2.1, IC3.41 (PA1), R12.1
STRAINREF: C8.1, IC3.44 (PA4), R15.1, R16.2
STRAIN_VCC: R2.2, R15.2, STRAIN.3
THIN: R20.2, THR.2
THROTTLE: IC3.2 (PA6), R20.1, R23.2
TX: IC3.33 (PE3), R35.1
VBAT: D1.A, MMUP.2
VIN: C6.+, D4.C, F1.2, R1.2, R29.2, U1.8 (VIN), VBUS.1
VIN_SENSE: IC3.3 (PA7), R1.1, R8.2

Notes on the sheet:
RED - GREEN - 5V
WHITE - PURPLE - GND
YELLOW - BLUE - DAT
1.25V
2.50V
Original HW has 6 pins
12V was added at PIN1, and all numbers are shifted one up.
Display Connector
H/L reversed for neater routing
Like you're ever gonna see these...
Halls moved to digital inputs. Internally pulled up, hall sensors sink.
100k = 12V DATA BUS
47k = 24V DATA BUS

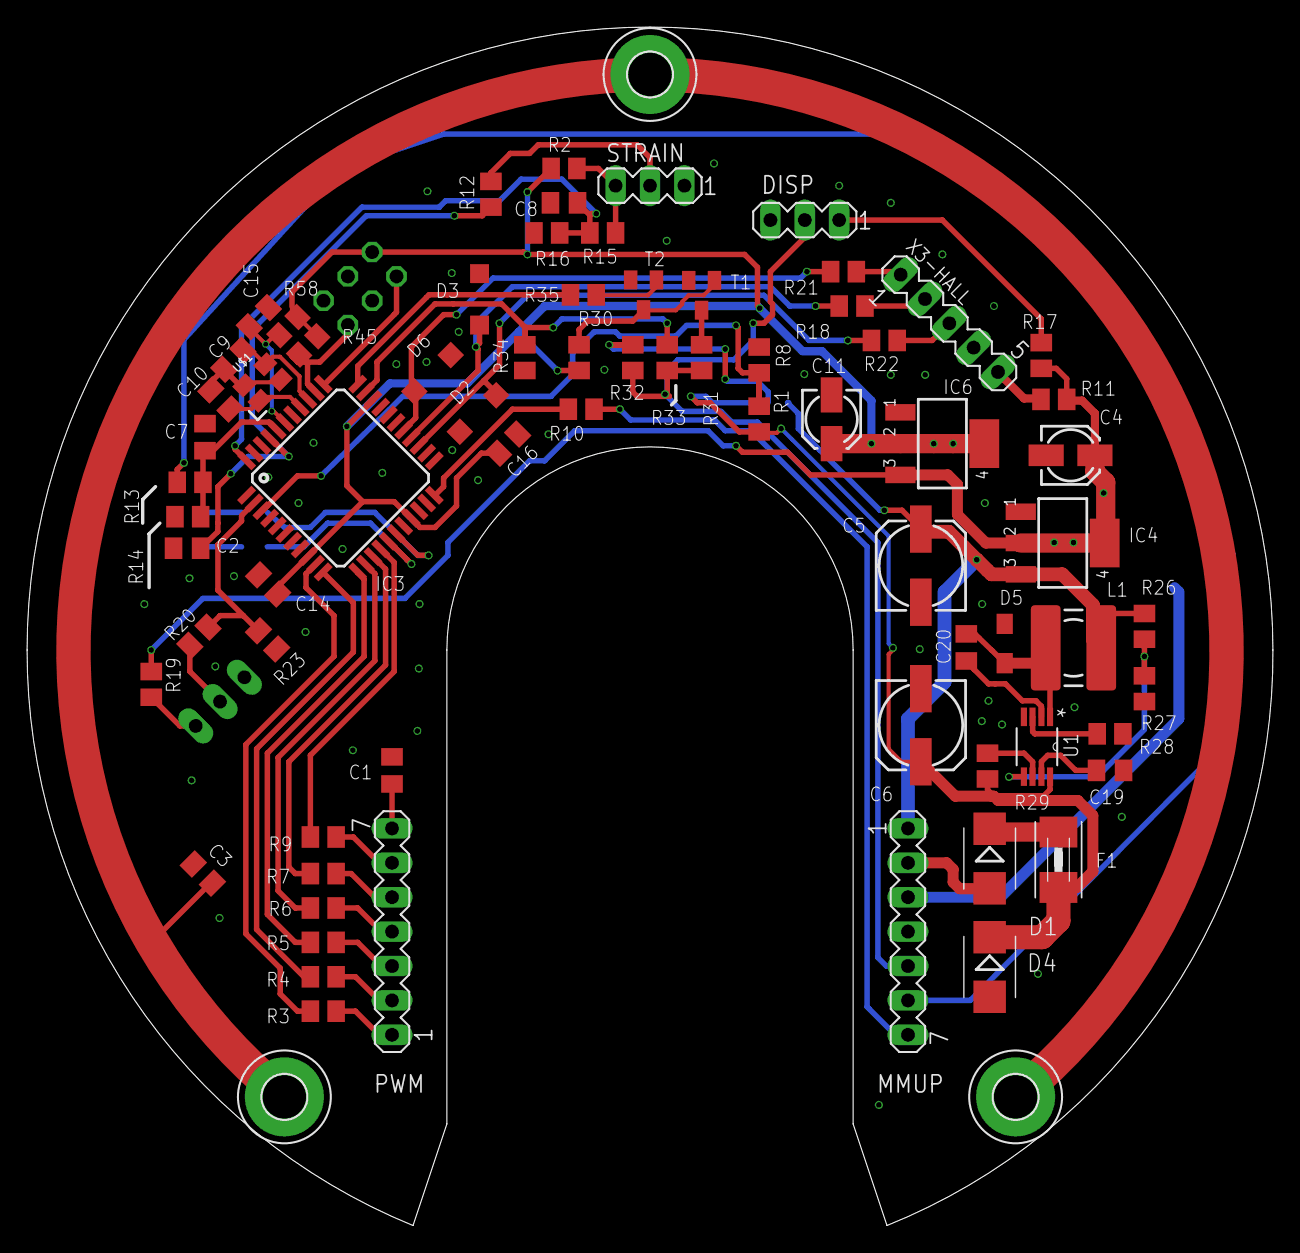
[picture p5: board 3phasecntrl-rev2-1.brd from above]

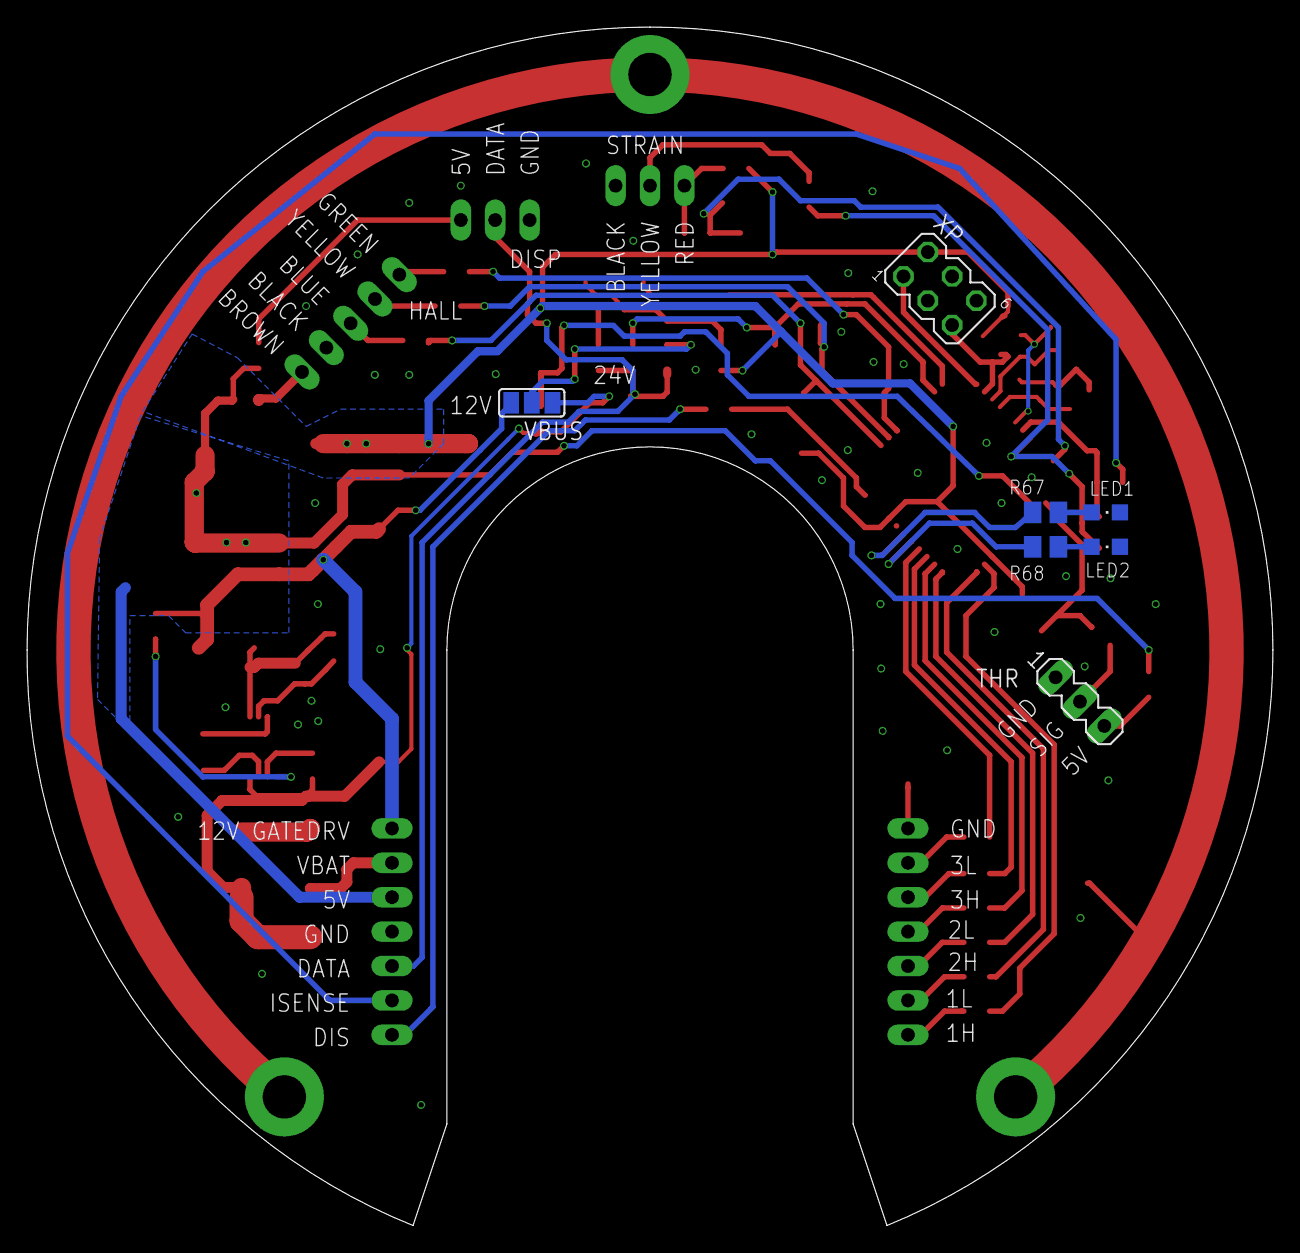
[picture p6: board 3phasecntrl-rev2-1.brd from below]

Board: 2 copper layers, 92.0 x 88.5 mm, 81 parts (7 on the bottom side), 63 nets.

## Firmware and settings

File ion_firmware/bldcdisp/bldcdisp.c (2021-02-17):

/*
	Created: 2014-06-23T17:07:46Z
	Author: D. Prins
		Infant - infant.tweakblogs.net
		mail: prinsje2004 at gmail

		File: bldcdisp.c
	Application running on Sparta ION Control Board.
	Responsible for generating motor drive signals and display communication.
	Features and hardware definitions are set/defined in app.h

	This code is released under GNU GPL v3:

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
	    You should have received a copy of the GNU General Public License
    along with this program.  If not, see <http://www.gnu.org/licenses/>.
*/

#define F_CPU 32000000UL
#include <util/delay.h>

#include <avr/io.h>
#include <stdio.h>
#include <stdint.h>
#include <stdbool.h>

#include <avr/interrupt.h>
#include "app.h"
#include "adc.h"
#include "uart.h"
#include "../fwcommon/eeprom.h"
#include "../../lib_ion/bowbus.h"


#define REF_1V0				ADC_REFSEL_INT1V_gc
//Some version of AVR studio may complain here, and wants this set to ADC_REFSEL_VCC_gc
#define REF_3V3				ADC_REFSEL_INTVCC_gc

//Absolute PWM limits.
#define PWM_MAX				420
#define PWM_SET_MAX			PWM_MAX - 15
#define PWM_MIN				35
#define PWM_SET_MIN			PWM_MIN //PWM_MIN+3

//Dynamic PWM limits.
volatile uint16_t pwm_set_min = PWM_SET_MIN;
volatile uint16_t pwm_set_max = PWM_SET_MAX;

bool flagsave = false;			//Set when settings need to be saved
settings_t eepsettings;			//The settings.

bool usehall = true;
bool use_throttle = false;		//Apply throttle.
bool use_pedalassist = true;		//Apply throttle.

bool use_brake = false;			//Apply brake
bool flag_keep_pwm = false;

bool flag_brake_lowrpm = false;	//Brake has turned lower mosfets on.

volatile uint8_t brake				= 0;	//0 = no regen, 100 = max regen.
volatile uint8_t throttle_prev		= 0;
volatile uint8_t throttle			= 0;
volatile uint8_t throttle_override  = 0;	//Override for testing.
volatile uint8_t pedal_signal_prev	= 0;
volatile uint8_t pedal_signal		= 0;
volatile uint8_t brake_level		= 0;	//Brake power

//Bitfields for status flags
#define STAT_OK					0x0000
#define STAT_THROTTLE_FAULT		0x0001
#define STAT_OVER_VOLTAGE		0x0002
#define STAT_UNDER_VOLTAGE		0x0004
#define STAT_REGEN_HIGH			0x0008
#define STAT_STOPPED			0x0010
#define STAT_USETHROTTLE		0x0020
#define STAT_HALL_FAULT			0x0040
#define STAT_BRAKE_FAULT		0x0080

//All the possible errors
#define STAT_ERROR_MASK			(STAT_THROTTLE_FAULT | STAT_BRAKE_FAULT | STAT_OVER_VOLTAGE | STAT_UNDER_VOLTAGE | STAT_REGEN_HIGH | STAT_STOPPED )

//Status bitmap
uint32_t status = 0;

//Functions:
void status_set(uint32_t);
void status_clear(void);
bool isfaultset(void);
void pwm_less(uint8_t by);
void pwm_more(uint8_t by);
void pwm_update(void);
void commute_start(void);
void commute_forward(void);
void commute_backward(void);

bool get_throttle(void);
bool get_brake(void);

//For Bowbus
bool bus_check_for_message(void);

uint16_t cnt_2 = 0;
uint8_t led_off_cnt = 0;
uint8_t flag_timer = 0;

#define HALL_MASK (PIN4_bm | PIN5_bm | PIN6_bm)

//Hall peaks
uint16_t hallhi = 0;
uint16_t halllo = 0;

uint8_t hall_state = 0;
uint8_t hall_prev = 0;
uint8_t flag_hall_changed = 0;

uint16_t pwm = PWM_SET_MAX;
uint16_t pwm_prev = PWM_SET_MAX;

uint8_t off = 0;	//Freewheel on/off.
uint8_t tie = 0;	//Tie low to GND.

uint8_t startup = 10;

//If you want the wheel to go the other way.
#define FORWARD 0
#define BACKWARD 1
uint8_t direction = BACKWARD;		//This is actually forward....

//Calibration value for strain sensor.
uint16_t strain_threshhold = 200;
uint8_t strain_cal_inc = 1;

//Strain sensor values.
int32_t ad_strain = 0;
int32_t ad_strain_sum = 0;
int32_t ad_strain_av = 500;		//Center around 500.

int16_t strain_min = 500;		//Self calibrating...
int16_t strain_max = 500;

uint8_t strain_gain = 4;		//Gain factor in throttle.

//If the strain signal registered, how long it should be on for.
uint16_t strain_cnt = 0;

uint32_t ad_temp_ref = 0;			//Factory reference.
uint32_t ad_temp = 0;
uint32_t ad_temp_sum = 0;
uint32_t ad_temp_av = 0;

uint32_t ad_throttle = 0;
uint32_t ad_brake = 0;

uint32_t ad_voltage = 0;
uint32_t ad_voltage_sum = 0;
uint32_t ad_voltage_av = 0;

int32_t ad_current = 0;
int32_t ad_current_sum = 0;		//Sum of current over meas_cnt time.
int32_t ad_current_av = 0;		//The final average, computed on display update.

int32_t power_av = 0;

uint16_t ad_current_regcnt = 0;
int32_t ad_current_regsum = 0;		//Average computed per commutation
int32_t ad_current_regav = 0;		//The average for the commutation loop.

uint16_t meas_cnt = 0;

int32_t ad_currentmin = 0;
int32_t ad_currentmax = 0;

//Get all analog samples on this board.
uint8_t ad_max_samples = 8;


uint16_t time_prev = 0;
uint16_t time_now = 0;
uint32_t time_comm = 0;

uint32_t time_comm_av = 0;
uint32_t time_comm_av_last = 0;

uint32_t commtime_sum = 0;	//Sum of commutation times.
uint32_t commtime_cnt = 0;	//Number of commutations within that period
uint32_t speed = 0;			//in kmh * 1000. So 10000 = 10.0 kmh

uint16_t cnt_commutations = 0;
uint16_t cnt_rotations = 0;

//Regulaton settings
uint8_t slope_throttle = 1;	//Rate at which PWM may increase for throttle.
uint8_t slope_brake = 10;		//Rate at which PWM may increase for brake.

//Throttle limits.
#define THROTTLE_DISC	100		//Throttle disconnected. //600 safe value
#define THROTTLE_LOW	730		//Lowest
#define THROTTLE_HIGH	2890	//Highest
#define THROTTLE_OVER	3900	//Too high //3100 safe value

uint16_t throttle_tick = 0;
bool throttle_cruise = false;

//Strain min and maximum recorded value.
int16_t highestforce = 0;
int16_t lowestforce = 0;

bowbus_net_s bus;

void init(void){
	PORTD.DIRSET = PIN0_bm;
	PORTC.DIRSET = PIN3_bm | PIN2_bm | PIN1_bm | PIN0_bm;
}

void clock_switch32MExt(void){
	/*Setup 32MHz clock to run from External 16MHz oscillator.*/
	OSC.XOSCCTRL |=  OSC_FRQRANGE1_bm | OSC_FRQRANGE0_bm | OSC_XOSCSEL3_bm | OSC_XOSCSEL1_bm | OSC_XOSCSEL0_bm;
	OSC.PLLCTRL =  OSC_PLLSRC1_bm | OSC_PLLSRC0_bm |OSC_PLLFAC1_bm ;
	OSC.CTRL |= OSC_XOSCEN_bm;
	while (!(OSC.STATUS & OSC_XOSCRDY_bm));
	OSC.CTRL |= OSC_PLLEN_bm;
	while (!(OSC.STATUS & OSC_PLLRDY_bm));
	CCP = CCP_IOREG_gc;
	CLK.CTRL = CLK_SCLKSEL_PLL_gc;
	OSC.CTRL &= (~OSC_RC2MEN_bm);
	PORTCFG.CLKEVOUT = (PORTCFG.CLKEVOUT & (~PORTCFG_CLKOUT_gm)) | PORTCFG_CLKOUT_OFF_gc;	// disable peripheral clock
}

void clock_switch32M(void){
	/*Setup clock to run from Internal 32MHz oscillator.*/
	OSC.CTRL |= OSC_RC32MEN_bm;
	while (!(OSC.STATUS & OSC_RC32MRDY_bm));
	CCP = CCP_IOREG_gc;
	CLK.CTRL = CLK_SCLKSEL_RC32M_gc;
	OSC.CTRL &= (~OSC_RC2MEN_bm);
	PORTCFG.CLKEVOUT = (PORTCFG.CLKEVOUT & (~PORTCFG_CLKOUT_gm)) | PORTCFG_CLKOUT_OFF_gc;	// disable peripheral clock
}

void init_pwm(void){
	//PIN direction:
	PORTC.DIRSET = 0xFF;
	//Setup PWM
	TCC0.CTRLA = TC_CLKSEL_DIV8_gc;
	TCC0.CTRLB = TC_WGMODE_SINGLESLOPE_gc;
	TCC0.PER = PWM_MAX;
	//Default PWM value
	TCC0.CCA = pwm_set_max;
	TCC0.CCB = pwm_set_max;
	TCC0.CCC = pwm_set_max;

	//HiRes extensions
	HIRESC.CTRLA = HIRES_HREN_TC0_gc;

	//Dead time:
#if(HARDWARE_VER == HW_CTRL_REV1)
	//Sparta ION Board has hardware deadtime.
	AWEXC.DTHS = 0;
	AWEXC.DTLS = 0;
#else
	AWEXC.DTHS = 1;
	AWEXC.DTLS = 1;
#endif

	AWEXC.STATUS = AWEX_DTHSBUFV_bm | AWEX_DTLSBUFV_bm | AWEX_FDF_bm;

#if(HARDWARE_VER == HW_CTRL_REV1)
	//This hardware has inverted high side inputs, so we'll invert them again.
	PORTC.PIN0CTRL = PORT_INVEN_bm;
	PORTC.PIN2CTRL = PORT_INVEN_bm;
	PORTC.PIN4CTRL = PORT_INVEN_bm;

	//The Low/High are also switched with respect to first board, it routed nicer.
#endif
}

#if(HARDWARE_VER == HW_CTRL_REV1)

void sector_0(void){
	AWEXC.OUTOVEN =  PIN0_bm | PIN1_bm;
	AWEXC.CTRL =  AWEX_DTICCAEN_bm;
	PORTC.OUTCLR = PIN0_bm | PIN1_bm | PIN2_bm | PIN3_bm |  PIN4_bm;
	PORTC.OUTSET = PIN5_bm;
}

void sector_1(void){
	AWEXC.OUTOVEN = PIN0_bm |  PIN1_bm;
	AWEXC.CTRL =  AWEX_DTICCAEN_bm;
	PORTC.OUTCLR = PIN0_bm | PIN1_bm |  PIN2_bm | PIN4_bm | PIN5_bm;
	PORTC.OUTSET = PIN3_bm;
}

void sector_2(void){
	AWEXC.OUTOVEN =  PIN4_bm| PIN5_bm;
	AWEXC.CTRL =  AWEX_DTICCCEN_bm;
	PORTC.OUTCLR = PIN0_bm | PIN1_bm |  PIN2_bm | PIN4_bm | PIN5_bm;
	PORTC.OUTSET = PIN3_bm;
}

void sector_3(void){
	AWEXC.OUTOVEN =  PIN4_bm| PIN5_bm;
	AWEXC.CTRL =  AWEX_DTICCCEN_bm;
	PORTC.OUTCLR =  PIN0_bm | PIN2_bm | PIN3_bm | PIN4_bm | PIN5_bm;
	PORTC.OUTSET = PIN1_bm;
}

void sector_4(void){
	AWEXC.OUTOVEN =  PIN2_bm | PIN3_bm;
	AWEXC.CTRL =  AWEX_DTICCBEN_bm;
	PORTC.OUTCLR = PIN0_bm | PIN2_bm | PIN3_bm | PIN4_bm | PIN5_bm;
	PORTC.OUTSET = PIN1_bm;
}

void sector_5(void){
	AWEXC.OUTOVEN =  PIN2_bm | PIN3_bm;
	AWEXC.CTRL =  AWEX_DTICCBEN_bm;
	PORTC.OUTCLR = PIN0_bm | PIN1_bm | PIN2_bm | PIN3_bm |  PIN4_bm;
	PORTC.OUTSET = PIN5_bm;
}
#else
void sector_0(void){
	AWEXC.OUTOVEN =  PIN0_bm | PIN1_bm;
	AWEXC.CTRL =  AWEX_DTICCAEN_bm;
	PORTC.OUTCLR = PIN0_bm | PIN1_bm | PIN2_bm | PIN3_bm |  PIN5_bm;
	PORTC.OUTSET = PIN4_bm;
}

void sector_1(void){
	AWEXC.OUTOVEN = PIN0_bm |  PIN1_bm;
	AWEXC.CTRL =  AWEX_DTICCAEN_bm;
	PORTC.OUTCLR = PIN0_bm | PIN1_bm |  PIN3_bm | PIN4_bm | PIN5_bm;
	PORTC.OUTSET = PIN2_bm;
}

void sector_2(void){
	AWEXC.OUTOVEN =  PIN4_bm| PIN5_bm;
	AWEXC.CTRL =  AWEX_DTICCCEN_bm;
	PORTC.OUTCLR = PIN0_bm | PIN1_bm |  PIN3_bm | PIN4_bm | PIN5_bm;
	PORTC.OUTSET = PIN2_bm;
}

void sector_3(void){
	AWEXC.OUTOVEN =  PIN4_bm| PIN5_bm;
	AWEXC.CTRL =  AWEX_DTICCCEN_bm ;
	PORTC.OUTCLR =  PIN1_bm | PIN2_bm | PIN3_bm | PIN4_bm | PIN5_bm;
	PORTC.OUTSET = PIN0_bm;
}

void sector_4(void){
	AWEXC.OUTOVEN =  PIN2_bm | PIN3_bm;
	AWEXC.CTRL =  AWEX_DTICCBEN_bm;
	PORTC.OUTCLR = PIN1_bm | PIN2_bm | PIN3_bm | PIN4_bm | PIN5_bm;
	PORTC.OUTSET = PIN0_bm;
}

void sector_5(void){
	AWEXC.OUTOVEN =  PIN2_bm | PIN3_bm;
	AWEXC.CTRL =  AWEX_DTICCBEN_bm;
	PORTC.OUTCLR = PIN0_bm | PIN1_bm | PIN2_bm | PIN3_bm |  PIN5_bm;
	PORTC.OUTSET = PIN4_bm;
}
#endif

void commute_start(void){
	//Set deadtime, HW specific
#if(HARDWARE_VER == HW_CTRL_REV1)
	AWEXC.DTHS = 0;
	AWEXC.DTLS = 0;
#else
	AWEXC.DTHS = 1;
	AWEXC.DTLS = 1;
#endif
	//Apply.
	AWEXC.STATUS = AWEX_DTHSBUFV_bm | AWEX_DTLSBUFV_bm | AWEX_FDF_bm;

	//Reset highside refresh thingy:
	TCD0.CNT = 0;
}

void switch_sector(uint8_t sect){
	switch(sect){
		case 0:
			sector_0();
			break;
		case 1:
			sector_1();
			break;
		case 2:
			sector_2();
			break;
		case 3:
			sector_3();
			break;
		case 4:
			sector_4();
			break;
		case 5:
			sector_5();
			break;
	}
}

void pwm_freewheel(void){
	PORTC.OUTCLR = PIN5_bm | PIN4_bm | PIN3_bm | PIN2_bm | PIN1_bm | PIN0_bm;
	//Dead time:
	AWEXC.OUTOVEN = 0;
	AWEXC.CTRL = 0;
}

/*
	Connect all lower side MOSFETs, it's like shorting the wires together.
	Better not do this while driving really fast.
*/
void tie_ground(void){
	PORTC.OUTCLR = PIN5_bm | PIN4_bm | PIN3_bm | PIN2_bm | PIN1_bm | PIN0_bm;
	//Dead time:
	AWEXC.OUTOVEN = 0;
	AWEXC.CTRL = 0;

	//Enable lower FETs
	#if(HARDWARE_VER == HW_CTRL_REV1)
		PORTC.OUTSET =  PIN5_bm |  PIN3_bm |  PIN1_bm;
	#else
		PORTC.OUTSET =  PIN4_bm |  PIN2_bm |  PIN0_bm;
	#endif
}

//Estimate the PWM value when freewheeling which would yield close to no current.
uint16_t estimate_pwm_byspeed(){
	int16_t pwm_est = 0;
#if((HARDWARE_VER == HW_BLDC_REV1)||(HARDWARE_VER == HW_BLDC_REV0))
	if (speed > 0){
		pwm_est = pwm_set_max - ((((pwm_set_max) - (pwm_set_min)) / 30) * (speed/10));

		if (pwm_est < pwm_set_min){
			pwm_est = pwm_set_min;
		}
		if (pwm_est > pwm_set_max){
			pwm_est = pwm_set_max;
		}
	}else{
		pwm_est = pwm_set_max;
	}
#else
	//Inverted PWM:
	if (speed > 0){
		pwm_est = pwm_set_min + (((uint16_t)speed*12UL)/10UL);

		if (pwm_est < pwm_set_min){
			pwm_est = pwm_set_min;
		}
		if (pwm_est > pwm_set_max){
			pwm_est = pwm_set_max;
		}
	}else{
		pwm_est = pwm_set_min;
	}
#endif
	return (uint16_t)pwm_est;
}
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
int main(void){
	//Run of the internal 32MHz oscillator.
	//clock_switch32M();
	//Run off the external 16MHz oscillator with 32MHz PLL.
	clock_switch32MExt();
	
	init_pwm();
	uart_init();
	bus_init(&bus);

	//Clear the AD settings.
	PORTA.DIR = 0;
	PORTA.OUT = 0;
	ADCA.CTRLA  = ADC_FLUSH_bm;
	ADCA.CTRLB  = 0;
	ADCA.REFCTRL  = 0;
	ADCA.EVCTRL  = 0;
	ADCA.PRESCALER  = 0;

	//Set PORTB as AD input
	PORTB.DIR = 0;
	PORTB.OUT = 0;

	//Setup a timer, just for counting. Used for bus message and timeouts.
	TCC1_CTRLA = TC_CLKSEL_DIV1024_gc;

	//Set up the RTC for speed timing.
	CLK.RTCCTRL = CLK_RTCSRC_RCOSC32_gc | CLK_RTCEN_bm;
	RTC.CTRL = RTC_PRESCALER_DIV1_gc;
	RTC.COMP = 32768;

	//A counter for 100% PWM timing.
	TCD0.CTRLA = TC_CLKSEL_DIV1024_gc;
	TCD0.PER = 320;
	TCD0.INTCTRLA = TC_OVFINTLVL_HI_gc;


	//Make sure to move the reset vectors to application flash.
	//Set the interrupts we want to listen to.
	CCP = CCP_IOREG_gc;
	PMIC.CTRL = PMIC_LOLVLEN_bm | PMIC_MEDLVLEN_bm |PMIC_HILVLEN_bm | PMIC_RREN_bm;

	//Enable interrupts.
	sei();

	//Set defaults:
	eepsettings.straincal = 200;
	eemem_read_block(EEMEM_MAGIC_HEADER_SETTINGS,(uint8_t*)&eepsettings, sizeof(eepsettings), EEBLOCK_SETTINGS1);

	//Apply settings...
	strain_threshhold = eepsettings.straincal;
	display.function_val5 = eepsettings.straingain;
	//strain_gain = eepsettings.straingain;

	//Startup hall state.
	hall_state = 0x04;
	get_hall();

	//Startup PWM value.
	pwm = PWM_SET_MIN;

	//Test
	/*
	motor.mode = 1;
	display.road_legal = false;
	display.function_val1 = 2;
	display.function_val2 = 5;
	*/
	//display.function_val1 = 2;

	uint8_t cnt_tm = 0;		//Used by TCC1
	uint8_t poll_cnt = 0;	//Used for polling the display.
	uint16_t pwm_lim = 0;	//PWM limit may change at higher speed.

	display.strain_th = strain_threshhold;

	//Two flags that can only be set.
	bool should_freewheel = true;
	bool force_commute = false;
	while(1){
		//Double check the PWM hasn't gone crazy:
		if (pwm < pwm_set_min){
			pwm = pwm_set_min;
		}
		if (pwm > pwm_set_max){
			pwm = pwm_set_max;
		}

		//Apply PWM settings.
		pwm_update();

		//Get halls sensors.
		if (!get_hall()){
			should_freewheel = true;
			status_set(STAT_HALL_FAULT);
		}

		//Commute or freewheel:
		if (should_freewheel){
			pwm_freewheel();
		}else if (force_commute){
			if (direction == FORWARD){
				commute_forward();
			}else{
				commute_backward();
			}

		}else if (flag_hall_changed){
			if (direction == FORWARD){
				commute_forward();
			}else{
				commute_backward();
			}
		}else{
			//pwm_freewheel();
		}

		//Remember...
		pwm_prev = pwm;

		//Reset
		should_freewheel = false;
		//force_commute = false;

		if (startup == 10){ //Just started
			//Setup PWM
			commute_start();
			pwm = estimate_pwm_byspeed();
			//Apply PWM settings.
			pwm_update();
		}

		if (display.online == false){
			should_freewheel = true;
		}
		if (motor.mode == 0){
			should_freewheel = true;
		}

		//Get voltage,current and whatever else.
		get_measurements();

		//Instantanious under and over voltage.
		if (ad_voltage > 3700){ //3900
			//Freewheel as fast as possible.
			pwm_freewheel();
			should_freewheel = true;
			status_set(STAT_OVER_VOLTAGE);
		}else if (ad_voltage < 1800){ //About 19 volts.
			//Freewheel as fast as possible.
			pwm_freewheel();
			should_freewheel = true;
			status_set(STAT_UNDER_VOLTAGE);
			pwm_less(200);pwm_less(200); //OMG!
		}

		//Regenning too hard:
		if (ad_current_regav < -1300){
			//Freewheel as fast as possible.
			//pwm_freewheel();
			//should_freewheel = true;
			//status_set(STAT_REGEN_HIGH);
			//startup = 3;
		}

		if (use_throttle){
			//Get the throttle value.
			if (!get_throttle()){
				status_set(STAT_THROTTLE_FAULT);
				should_freewheel = true;
			}
		}
		if (use_brake){
			//Use the brake too:
			if (get_brake()){
				if (use_brake){
					throttle_cruise = false;
					throttle_tick = 0;
				}else{
					if (throttle == 0){ //< 5
						should_freewheel = true;
					}
				}
			}else{
				status_set(STAT_BRAKE_FAULT);
				should_freewheel = true;
			}
		}

		//Maybe it'll run without at some point...
		if (usehall){
			//Timer:
			if (flag_hall_changed){
				//Toggle blue led:
				PORTC.OUTTGL = PIN7_bm;

				//compute time:
				time_now = RTC.CNT;
				time_comm = time_now;
				//Running average.
				time_comm_av += time_comm;
				time_comm_av >>= 1;

				commtime_sum+= time_comm;
				commtime_cnt++;
				cnt_commutations++;

				//Reset timer.
				RTC.CNT = 0;

				//Computer average current in this time:
				if (ad_current_regcnt > 0){
					ad_current_regav = ad_current_regsum / (int32_t)ad_current_regcnt;
				}else{
					ad_current_regav = ad_current;
				}

				//Values reset in next if-statement.
			}

			//Allowed to go faster if the commutation time is guaranteed to switch fast enough.
			if ((time_comm_av < 350)&&display.online && (display.function_val2==9)){
				#if((HARDWARE_VER==HW_BLDC_REV0)||(HARDWARE_VER==HW_BLDC_REV1))
				//TCD0 is used in case the motor suddenly stops. Capacitors are 100uF/16V
				pwm_set_min = 0;
				#else
				//PWM is inverted on this board.
				pwm_set_max = PWM_SET_MAX;
				#endif
			}

			//PWM limit for braking
			pwm_lim = pwm_set_max -  (display.function_val3 * 10);
			if (pwm_lim < pwm_set_min){
				pwm_lim = pwm_set_min;
			}else if (pwm_lim > pwm_set_max){
				pwm_lim = pwm_set_max;
			}

			//That's really slow.
			if (RTC.CNT> 5000){
				speed = 0;
			}

			//Minimum response time
			if (flag_hall_changed) {


				//Clear current sum:
				ad_current_regcnt = 0;
				ad_current_regsum = 0;

				RTC.CNT = 0;
			}

			//Control loop
			if ((flag_hall_changed) || (TCC1.CNT > 450)){
				//Clear hall flag if it was set.
				flag_hall_changed = false;
				if (!off){
					//If brake is enabled:
					if (use_brake){
						if (brake > 5){
							//Regenning is a bit harder. The amount of strength decreases if PWM is too high.
							//Brake is current limited.
							//At low speed, ovverride PWM settings
							if (speed < 150){
								pwm_lim = pwm_set_max;
							}

							if ((ad_current_regav + 169) > (((int16_t)brake)*-12)){  //100 * 10 -> current of about -8 Amp
								//More power: inc PWM

								//Use the speed average as a voltage estimate for the motor.
								//24V will give an unloaded speed of 350 (35.0kmh)
								//If we're doing 10km/h, the motor is at 7V approx, 30% duty cycle.

								if (pwm < pwm_lim){
									pwm_less(slope_brake);
								}

							}else{
								//Back off
								pwm_more(slope_brake);
							}
							//Voltage limits
							if (ad_voltage > 3600){
								pwm_more(slope_brake/2);
							}
							if (ad_voltage > 3700){
								pwm_more(slope_brake/2);
							}
						}
					}
					if (use_throttle){
						//Undo brake :
						if (flag_brake_lowrpm){
							off = false;
							tie = false;
							status_clear();
							flag_brake_lowrpm = false;
						}

						if (throttle > 5){
							//Voltage limits
							if (ad_voltage < 1950){
								pwm_less(slope_throttle*2);
							}
							if (ad_voltage < 1900){
								pwm_less(slope_throttle*2);
							}

							//Current measures this commutation cycle.
							int32_t regulation = ad_current_regav;

							//Fixed calibration. Regulation value of 100 = 1 Amp
							#if(HARDWARE_VER == HW_CTRL_REV1)
							regulation += 1749;
							regulation *= 1000;
							regulation /= 286;
							regulation -= 34;
							#else
							regulation += 169;
							regulation *= 100;
							regulation /= 75;
							regulation += 18;
							#endif

							//Target current.
							int16_t target = ((int16_t)(throttle*15)/10)*2*(int16_t)motor.mode;

							//Current regulation
							if (1){
								if (regulation < (target/4)){ //200 * 0-5
									pwm_more((speed/10)+1);
								}else if (regulation < (target/2)){
									//More power
									pwm_more(slope_throttle*2);
								}else if (regulation < target){
									//More power
									pwm_more(slope_throttle);
								}else{
									//Back off
									pwm_less(slope_throttle);
								}
							}
						}
					}

					if (use_pedalassist){
						//Compute amount of throttle 0-100% from strain signal
						pedal_signal_prev = pedal_signal;
						uint16_t pedal_new = 0;

						if (ad_strain_av > strain_threshhold){
							//Get the pedal value.
							if (ad_strain_av-strain_threshhold < 100){
								pedal_new = ad_strain_av-strain_threshhold;
								pedal_new *= strain_gain;
								if (pedal_new > 100){
									pedal_new = 100;
								}
							}else{
								pedal_new = 100;
							}

							//Reset timer.
							if (pedal_new >= pedal_signal){
								strain_cnt = 120;
							}else if (pedal_new > 20){
								strain_cnt = 60;
							}
						}
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

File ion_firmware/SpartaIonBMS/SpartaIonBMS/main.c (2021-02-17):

/*
 * SpartaIonBMS.c
 *
 * Created: 29-8-2020 14:41:45
 * Author : T. Ligeon
 *	
 *  BQ34Z100 = C0/C1
 *	BOW_UART = PE2/PE3
 *	RTC I2C = PE0/PE1
 */ 

// Defines

// Includes
#include <avr/io.h>
#include <avr/sleep.h>
#include <stdio.h>
#include "app.h"
#include "uart.h"
#include "twi_master_driver.h"
#include "bq34z100.h"



//For Bowbus
bowbus_net_s bus;
bool bus_check_for_message(void);
char bow_buffer[1024];
uint32_t bowStrSize=0;

// Main Variables
TWI_Master_t i2c_handler_BQ34Z100;
TWI_Master_t i2c_handler_RTC;

adc_readings_t adcData;
bq_readings_t bqData;

static uint8_t cnt_tm = 0;			//Used by TCC1
static uint8_t sleepDelayTimer=0;	// Used for sleeping

static uint8_t oldDisplayStatus=0;

// Read signature byte for ADC Calibration
uint8_t ReadSignatureByte(uint16_t Address)
{
	NVM_CMD = NVM_CMD_READ_CALIB_ROW_gc;
	uint8_t Result;
	Result = pgm_read_byte((uint8_t *)Address);
	NVM_CMD = NVM_CMD_NO_OPERATION_gc;
	return Result;
}

//Initialize all IO.
void _init_GPIO(void){
	
	PORTA.DIRCLR = MIDPOINT_V_PIN | VIN_SENSE_PIN | CHG_PRESENT_PIN | PACK_TEMP_PIN | PCB_TEMP_PIN;
	PORTC.DIRCLR = BQ34Z100_ALERT_PIN;
	PORTC.DIRSET = LIGHT_EN_PIN | MOT_PWR_EN_PIN | CHG_PWR_EN_PIN | LED1_PIN | LED2_PIN | SDA_C_PIN | SCL_C_PIN;
	PORTD.DIRCLR = RTC_INT_PIN;	
	PORTE.DIRSET = SDA_E_PIN | SCL_E_PIN | BOW_TX_PIN;
	PORTE.DIRCLR = BOW_RX_PIN;
	
	
	// Enable interrrupt for Charge Detection
	//CHG_PRESENT_PORT.PIN2CTRL = PORT_ISC_RISING_gc;
	//CHG_PRESENT_PORT.INT1MASK = CHG_PRESENT_PIN;
	//CHG_PRESENT_PORT.INTCTRL = PORT_INT1LVL_LO_gc;
	
	
	// Enable pullups on all unused pins to reduce sleep power consumption.
	PORTA.PIN5CTRL = PORT_OPC_PULLUP_gc;
	PORTA.PIN6CTRL = PORT_OPC_PULLUP_gc;
	PORTA.PIN7CTRL = PORT_OPC_PULLUP_gc;
	PORTB.PIN0CTRL = PORT_OPC_PULLUP_gc;
	PORTB.PIN1CTRL = PORT_OPC_PULLUP_gc;
	PORTB.PIN2CTRL = PORT_OPC_PULLUP_gc;
	PORTB.PIN3CTRL = PORT_OPC_PULLUP_gc;
	PORTD.PIN0CTRL = PORT_OPC_PULLUP_gc;
	PORTD.PIN1CTRL = PORT_OPC_PULLUP_gc;
	PORTD.PIN3CTRL = PORT_OPC_PULLUP_gc;
	PORTD.PIN4CTRL = PORT_OPC_PULLUP_gc;
	PORTD.PIN5CTRL = PORT_OPC_PULLUP_gc;
	PORTD.PIN6CTRL = PORT_OPC_PULLUP_gc;
	PORTD.PIN7CTRL = PORT_OPC_PULLUP_gc;
	
}

void _init_adc(void){
	
	ADCA.CALL = ReadSignatureByte(0x20) ; //ADC Calibration Byte 0
	ADCA.CALH = ReadSignatureByte(0x21) ; //ADC Calibration Byte 1

	ADCA.CTRLB = ADC_RESOLUTION_12BIT_gc | ADC_CONMODE_bm; //12 Bit, Signed Conversion
	ADCA.REFCTRL = 	ADC_REFSEL_INTVCC_gc; // VCC/1.6
	ADCA.PRESCALER   = ADC_PRESCALER_DIV4_gc; 
	
	ADCA.CH0.MUXCTRL = ADC_CH_MUXPOS_PIN0_gc;		//Midpoint Channel
	ADCA.CH0.CTRL = ADC_CH_GAIN_1X_gc | ADC_CH_INPUTMODE_SINGLEENDED_gc;
	
	ADCA.CH1.MUXCTRL = ADC_CH_MUXPOS_PIN1_gc;		//Pack Voltage Channel
	ADCA.CH1.CTRL = ADC_CH_GAIN_1X_gc | ADC_CH_INPUTMODE_SINGLEENDED_gc;
	
	ADCA.CH2.MUXCTRL = ADC_CH_MUXPOS_PIN3_gc;		//Pack Temp Channel
	ADCA.CH2.CTRL = ADC_CH_GAIN_1X_gc | ADC_CH_INPUTMODE_SINGLEENDED_gc;
	
	ADCA.CH3.MUXCTRL = ADC_CH_MUXPOS_PIN4_gc;		//PCB Temp Channel
	ADCA.CH3.CTRL = ADC_CH_GAIN_1X_gc | ADC_CH_INPUTMODE_SINGLEENDED_gc;
	
	ADCA.CTRLA  = ADC_ENABLE_bm;
}

void _init_peripherals(void){
	//Setup a timer, just for counting. Used for bus message and timeouts.
	TCC1_CTRLA = TC_CLKSEL_DIV1024_gc;
	
	//Init USART for BOW bus
	uart_init();
	bus_init(&bus);
	
	//Init I2C for BQ34Z100,
	TWI_MasterInit(&i2c_handler_BQ34Z100,&BQ34Z100_I2C,TWI_MASTER_INTLVL_LO_gc,I2C_BAUDSETTING);
	//Init I2C for RTC,
	//TWI_MasterInit(&i2c_handler_RTC,&BQ34Z100_I2C,TWI_MASTER_INTLVL_LO_gc,I2C_BAUDSETTING);
	
}

void clock_switch32MInt(void){
	/*Setup clock to run from Internal 32MHz oscillator.*/
	OSC.CTRL |= OSC_RC32MEN_bm;
	while (!(OSC.STATUS & OSC_RC32MRDY_bm));
	CCP = CCP_IOREG_gc;
	CLK.CTRL = CLK_SCLKSEL_RC32M_gc;
	OSC.CTRL &= (~OSC_RC2MEN_bm);
	PORTCFG.CLKEVOUT = (PORTCFG.CLKEVOUT & (~PORTCFG_CLKOUT_gm)) | PORTCFG_CLKOUT_OFF_gc;	// disable peripheral clock
}

void clock_switch32MExt(void){
	/*Setup 32MHz clock to run from External 16MHz oscillator.*/
	OSC.XOSCCTRL |=  OSC_FRQRANGE1_bm | OSC_FRQRANGE0_bm | OSC_XOSCSEL3_bm | OSC_XOSCSEL1_bm | OSC_XOSCSEL0_bm;
	OSC.PLLCTRL =  OSC_PLLSRC1_bm | OSC_PLLSRC0_bm |OSC_PLLFAC1_bm ;
	OSC.CTRL |= OSC_XOSCEN_bm;
	while (!(OSC.STATUS & OSC_XOSCRDY_bm));
	OSC.CTRL |= OSC_PLLEN_bm;
	while (!(OSC.STATUS & OSC_PLLRDY_bm));
	CCP = CCP_IOREG_gc;
	CLK.CTRL = CLK_SCLKSEL_PLL_gc;
	OSC.CTRL &= (~OSC_RC2MEN_bm);
	PORTCFG.CLKEVOUT = (PORTCFG.CLKEVOUT & (~PORTCFG_CLKOUT_gm)) | PORTCFG_CLKOUT_OFF_gc;	// disable peripheral clock
}

void _unit_Test(void){
	/*
		Functional Description:
		Used to test PCB actuators.
		Toggle Relay 1,
		Toggle LED 1
		Toggle Relay 2,
		Toggle Led 2,
	*/ 	
	LED1_PORT.OUTSET = LED1_PIN;
	_delay_ms(500);
	LED1_PORT.OUTCLR = LED1_PIN;
	_delay_ms(500);
	LED2_PORT.OUTSET = LED2_PIN;
	_delay_ms(500);
	LED2_PORT.OUTCLR = LED2_PIN;
	_delay_ms(500);
	MOT_PWR_EN_PORT.OUTSET = MOT_PWR_EN_PIN;
	_delay_ms(500);
	MOT_PWR_EN_PORT.OUTCLR = MOT_PWR_EN_PIN;
	_delay_ms(500);
	CHG_PWR_EN_PORT.OUTSET = CHG_PWR_EN_PIN;
	_delay_ms(500);
	CHG_PWR_EN_PORT.OUTCLR = CHG_PWR_EN_PIN;
	_delay_ms(500);
}

uint8_t _read_adc(struct adc_readings_t* adc_data){
	// THIS IS NOT YET FUNCTIONAL
	//uint8_t errorFlag=0;
	
	ADCA.CTRLA |= ADC_CH0START_bm | ADC_CH1START_bm | ADC_CH2START_bm | ADC_CH3START_bm;
	while(ADCA.INTFLAGS != 0x0F){printf("ADC Not done!\n"); _delay_ms(100);} // Wait for ADC channel conversions
	
	int16_t adc0Res = ADCA.CH0RES;
	int16_t adc1Res = ADCA.CH1RES;
	int16_t adc2Res = ADCA.CH2RES;
	int16_t adc3Res = ADCA.CH3RES;
	
	float adcREF = 3.3/1.6;
	uint16_t adcRES = 2047;
	
	
	//Run scalings on these values.
	adc_data->midpointV = (adcREF/adcRES)*adc0Res * 11.0;// / 2047 ;
	adc_data->vinSenseV = (adcREF/adcRES)*adc1Res * 22.28;// * v_divider / 2047; 
	adc_data->packTempC = adc2Res/22.7;//INT16_MAX) * pack_c_divider; 
	adc_data->pcbTempC = adc3Res/56.3;//INT16_MAX) * pcb_c_divider;
	
	//float ntcR = adc2Res / ((adcRES/adcREF) * 3.3) 
	
	//float steinhart;
	//steinhart = average / THERMISTORNOMINAL;     // (R/Ro)
	//steinhart = log(steinhart);                  // ln(R/Ro)
	//steinhart /= BCOEFFICIENT;                   // 1/B * ln(R/Ro)
	//steinhart += 1.0 / (TEMPERATURENOMINAL + 273.15); // + (1/To)
	//steinhart = 1.0 / steinhart;                 // Invert
	//steinhart -= 273.15;                         // convert to C
	
	//Run Sanity/Error checks on values, and return error flags accordingly
	//if(adc_data->vinSenseV < PACK_V_MIN){}
	//if(adc_data->vinSenseV > PACK_V_MAX){}
	//if(adc_data->midpointV < MID_V_MIN){}
	//if(adc_data->midpointV > MID_V_MAX){}
	//if((adc_data->vinSenseV - adc_data->midpointV) - adc_data->midpointV > PACK_D_MAX || (adc_data->vinSenseV - adc_data->midpointV) - adc_data->midpointV < -PACK_D_MAX ){}
	
	//if(adc_data->packTempC > PACK_C_MAX){}
	//if(adc_data->pcbTempC > PCB_C_MAX){}
	
	//Watchdog on ADC reading.
	
	
	return 0;
}
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

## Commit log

2020-07-07 3phasecntrl-rev-2-1 added. Crystal bijgebeund
    [3phasecntrl-rev2-1.brd, 3phasecntrl-rev2-1.sch, BOM_LCSC_3phasecntrl-rev2-1.xlsx]
2020-07-08 Voltage working on CU3, Current To be verified
2020-08-01 Added rev1.0 of Banana BMS.
    [BMS-banana-rev1-0.brd, BMS-banana-rev1-0.sch]
2021-02-17 Add BMS to Bootloader and 16MHz crystal.
2021-02-17 Add initial Semi-Working BMS firmware
2021-02-17 Add BMS to bootloader

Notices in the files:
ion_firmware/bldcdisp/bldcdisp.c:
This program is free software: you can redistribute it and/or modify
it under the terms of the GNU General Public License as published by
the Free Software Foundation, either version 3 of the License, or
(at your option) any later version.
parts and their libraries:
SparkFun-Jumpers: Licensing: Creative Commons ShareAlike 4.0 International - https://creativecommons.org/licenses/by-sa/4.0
